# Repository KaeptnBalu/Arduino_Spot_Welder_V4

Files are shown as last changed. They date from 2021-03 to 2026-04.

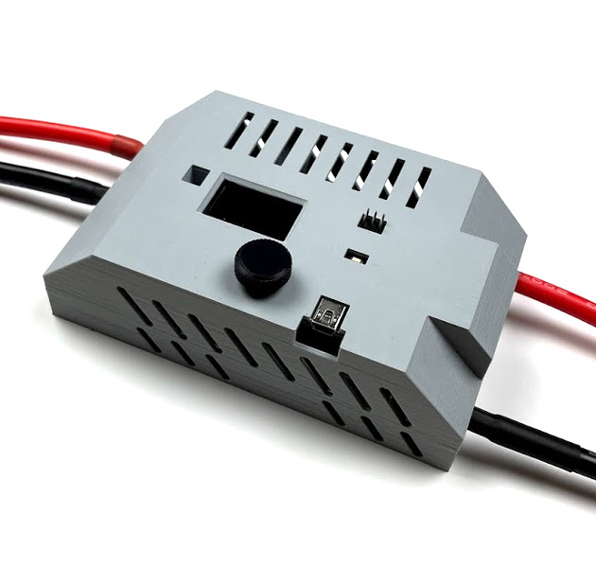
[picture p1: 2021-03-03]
Parts/Spot_Welder_V4_Case/case_kit_v4.jpg

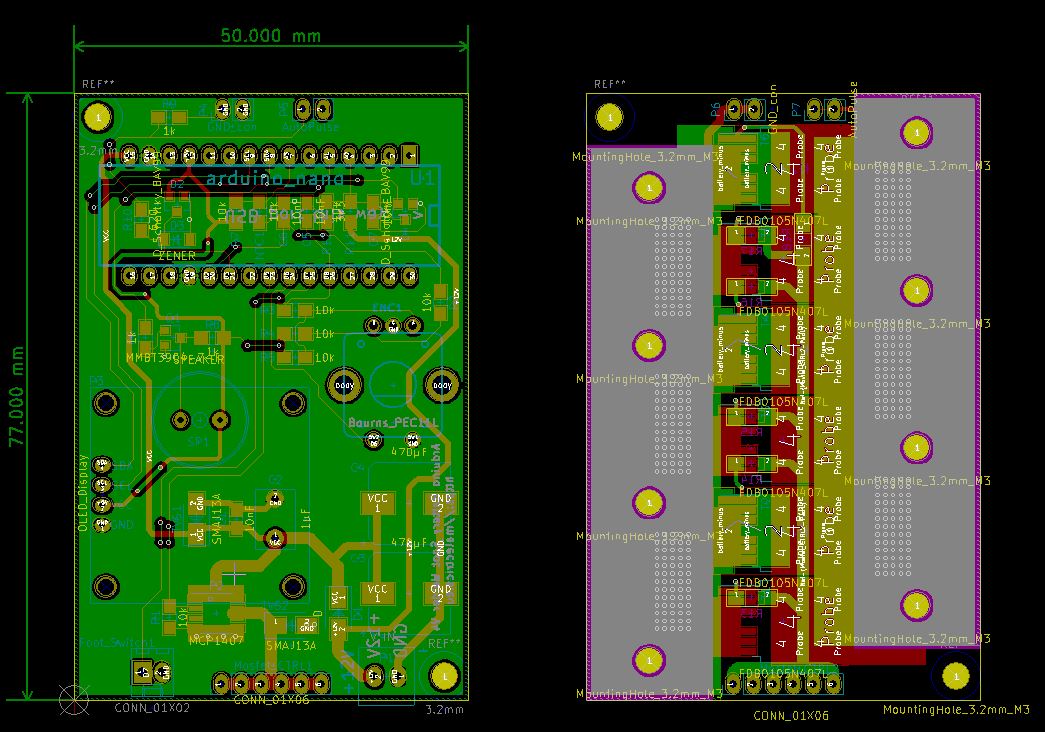
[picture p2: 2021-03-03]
KiCAD_PCB_Files/Spot_Welder_V4_PCB_Layout.JPG

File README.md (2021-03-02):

# Arduino_Spot_Welder_V4
This is the latest V4 of the Arduino Spot Welder. The previous V3 can be found here https://github.com/KaeptnBalu/Arduino_Spot_Welder_V3

An Arduino based Spot Welder for battery welding

    Build Guide: Car Bundle: https://malectrics.eu/v4-car-battery-bundle-assembly-instructions/ 
                 Lipo Bundle:https://malectrics.eu/v4-lipo-battery-bundle-assembly-instructions/
    Introduction Video: coming soon (Video for previuos V3 https://www.youtube.com/watch?v=CNmvx2JSCvA)
    Project Homepage: https://malectrics.eu/

Improvements in V4:

- Buzzer: With the buzzer alarms will not only be displayed on the screen but also be audible for the user. This makes it much easier to notice an alarm while working with the welder.    
- Temperature Sensor: The temperature sensor will trigger an alarm and disable welding when temperature reaches 65°C to protect the welder from overheating.
- additional 470µF Capacitor: With now two 470µF capacitors it is possible to use weld times up to 100 – 150ms without the risk of the Arduino Nano rebooting. The reboot could happen in V3 at very long weld times because the voltage at the Arduino Nano dropped to low dring the weld.  
- SMD Mosfet Driver: the mosfet driver chip has been changed from the through hole version that was plugged in a socket to a SMD version that is directly soldered to the pcb. The SMD version eliminates eventual contact problems that could happen with the through hole version when it was not plugged in the socket correctly.
- SMD Mosfets: The mosfets have been changed from through hole version to SMD. That will eliminate the problem of failing mosfet legs in V3 on very high currents.
- new aluminum parts: there are still two aluminum parts used on the mosfet board but the parts are just straight and both the same size. This makes producing or modding them for DIY users much easier.    
- Stronger Protection Diodes: The protection diodes on the bottom of the mosfet board have been changed to a much stronger version. They are rated for the same current as the ones in V3 but can take much higher short peak amps and have better heat dissipation because they are phisically bigger.

This Spot Welder can be used to weld 18650 batteries. It uses a 12V car battery as welding current supply. Typically one 60Ah 600A battery delivers enough current to get good welds with 0.15mm - 0.2mm nickel strips. For thicker nickel strips maybe you will need bigger battery or two in paralell. (Maximum 800A total)

The Welder generates a double pulse, where the first one is 12% of the time of the second one by default. Pulse time of the main pulse is adjustable by the rotary encoder and displayed on the screen in ms so you can exactly adjust the time. Its adjustable from 1 … 100 mS by default. (adjustable up to 500ms in the system menu)

If you want to download the project click on "clone or download" on this page. Downloading single files sometimes seems to cause some files to be corrupted while downloading.

You can get parts to build your own Spot Welder or prebuilt kits at https://malectrics.eu/

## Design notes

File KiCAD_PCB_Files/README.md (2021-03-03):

These are the pcb files for the Spot welder V4

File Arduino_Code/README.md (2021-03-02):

This is the Arduino Code for the Spot Welder V4. Do not use it with the older V2 or V3 pcbs. It is not compatible with these.

You need to have the Ardafruit_GFX library and the Ardafruit_SSD1306 library installed in your Arduino IDE to sucessfully compile the Code.

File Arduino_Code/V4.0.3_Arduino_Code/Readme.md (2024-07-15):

This is the V4.0.3 Arduino Code for the Arduino Spot Welder.

Improvements:
 - updated the menue structure 
 - added weld activation sound 
 - added a sound in auto pulse mode when both welding tips touch the nickel
 - sound can be switched on and off in the menue

After updating to this version please perform a "Full Reset" in the system menue of the welder to ensure proper functionality.

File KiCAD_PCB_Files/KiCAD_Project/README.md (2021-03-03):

These are the KICAD project files for the Arduino Spot Welder V4

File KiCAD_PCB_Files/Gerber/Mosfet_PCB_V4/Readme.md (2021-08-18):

These are the Gerber files for the Mosfet PCB V4. Please order it with 4oz copper layer at the pcb manufacturer because it needs to take a lot of current.

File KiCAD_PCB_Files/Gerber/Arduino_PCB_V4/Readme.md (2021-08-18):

These are the gerber files for the Arduino PCB V4. This one can be ordered with the standard 1oz copper layer.

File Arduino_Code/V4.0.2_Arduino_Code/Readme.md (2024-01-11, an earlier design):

This is the V4.0.2 Arduino Code for the Arduino Spot Welder.

Improvements:
- minor code improvements

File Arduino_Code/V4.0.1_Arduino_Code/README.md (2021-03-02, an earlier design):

This is the initial release of the redesigned V4.0.1 Arduino Code for the Arduino Spot Welder.

Improvements:
- adjust Code to work with Spot Welder V4
- add Buzzer routines
- add temperature sensor routines

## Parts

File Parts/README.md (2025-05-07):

These are the parts you need to buy for building the Spot Welder V4 from scratch. With the Mouser.com Shop Link you can directly ad all electronic component parts to your shopping cart.

Not included in the Mouser shopping cart link:

    1x Arduino Nano
    1x OLED Display

You can get ready made welding cables, aluminum parts and pcb sets at www.malectrics.eu if you dont want to make them yourself.

# BOM (Bill of materials) - electronic components

|Quantity |PCB Reference |Name |Mouser.com Part Number |
|---|---|---|---|
|6 |IRFS7430TRL7PP |Mosfet IRFS7430TRL7PP 40V 522A |942-IRFS7430TRL7PP |
|1 |MCP1407 |Mosfet Driver MCP1407-E/SN |579-MCP1407-E/SN |
|1 |Bourns_PEC11L |Rotary Encoder |652-PEC11L4220FS0015 |
|2 |U1 Arduino Nano |1x15 Pol Female Pin Header |992-15FX1-254MM |
|1 |Mosfet_CTRL2 |1x8 Pol Female Pin Header |437-8018700810001101 |
|2 |P6,P7 |1x2 Pol Female Pin Header |437-8018700210001101 |
|1 |OLED_Display |1x4 Pol Female Pin Header |517-974-01-04-RK |
|1 |Mosfet_CTRL1, P4, P5  |1x16 Pol Male Pin Header |538-22-28-4160 |
|1 |Foot_Switch1 |PCB connector 2pin |710-61900211121 |
|1 |P1 |Terminal Block |710-691214110002 |
|1 |D1 |SMD-Schottky 60V 1A |750-CDBA160-G |
|1 |Zener D3 |SMD Zener diode 4,3V 0,5W |78-MMSZ4687-E3-08 |
|2	 |D2,D4	 |Schottky BAV99	 |78-BAV99-E3-08 |
|4	 |TVS3,TVS4,TVS5	 |TVS Diode 15,6V 7kW	 |576-SLD8S14A |
|1	 |TVS1,TVS2	 |TVS Diode 14,4V 400W	 |621-SMAJ13A-13-F |
|1	 |C2	 |film capacitor 1 µF RM5	 |505-MKS2C041001FMSSD |
|2 |C3,C4 |electrolytic capacitor 470µF 25V |647-UWT1E471MNL1S |
|4 |C1, C5, C6, C7 |ceramic capacitor 0,01µF SMD |80-C0805C103J5R |
|1 |Q1 |Bipolartransistor 200mA |621-MMBT3904-F |
|1 |SP1 |Piezzo Speaker |810-PS1240P02BT |
|1 |NTC1 |NTC Thermistor |81-NCP21XV103J03RA |
|10 |R1;R2,R3,R4,R5,R7,R11 |Resistor 0805 SMD  10 kOhm |603-RC0805FR-0710KL |
|10 |R6,R8,R9 |Resistor 0805 SMD  1 kOhm |603-RC0805FR-071KL |
|10 |R10 |Resistor 0805 SMD  620 Ohm |603-RC0805FR-07620RL |
|10 |R12 |Resistor 0805 SMD  3,3 kOhm |603-RC0805FR-133K3L |
|10 |R13 … R18 |Resistor 1206 SMD  30 Ohm |603-RC1206FR-0730RL |

## Other Parts - Mechanical Parts - Optional Parts

| Quantity | Name | Description | Link / Where to buy |
|---|---|---|---|
| 1 | Arduino Nano | | [Banggood](https://ban.ggood.vip/15P6G)|
| 1 | OLED Diplay 0,96" 128x64 | take care of correct pinout (GND - VCC - SCL - SDA) | [Banggood](https://ban.ggood.vip/15P6J) |
| 1 | Alu 90x15x4mm | see alu_template.pdf | local hardware Store or  https://malectrics.eu/  | 
| 8 | M3x8 screw + nuts | for Alu Parts assembly | local hardware store |
| 2 | M3x20 screw | to screw pcbs together | local hardware store |
| 6 | M3 Nylon Nuts | to screw pcbs together | Ebay or Aliexpress |
| 1 | 1m 10 mm² - 16mm² flexible silicone cable | for 2pcs 0,5m welding cables | Ebay or Aliexpress |
| 1 | 0,1m 10mm² - 16mm² solid copper wire | for the welding tips | local hardware store or welding tips from https://malectrics.eu/ |
| 2 | cable shoe for 10 mm² or 16mm2 | for welding cable | local hardware store or https://malectrics.eu/ |
| 2 | cable connector for 10 mm² or 16mm2 | welding tip connection to the welding cables | local hardware store or https://malectrics.eu/ |
| 1 | battery terminals | for car battery | local hardware store or https://malectrics.eu/ |
| 1 | PCB Set | Arduino + Mosfet PCB | https://malectrics.eu/ |
| 2 | nylon spacers M2 x 12mm + M2x5 screws for OLED display | OPTIONAL | Ebay or Aliexpress |
| 1 | Foot Switch | OPTIONAL | https://malectrics.eu/ |
| 1 | 3d printed case | OPTIONAL | https://malectrics.eu/ or [Github](https://github.com/KaeptnBalu/Arduino_Spot_Welder_V4/tree/main/Parts/Spot_Welder_V4_Case) |
| 1 | 300A Fuse | OPTIONAL | https://malectrics.eu/

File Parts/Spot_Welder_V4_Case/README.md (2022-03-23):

These are the CAD files for the case. You can use these if you want to modify the case for your needs. The case was designed in Autodesk Fusion 360.
Ready printed case with acessories can be bought here: https://malectrics.eu/product/arduino-spot-welder-v4-case-kit-copy/

Additional hardware you need to mount the welder and the ANL 300A fuse in the case:

- 30x30x10mm 12V fan
- 4pcs M3x16 screws
- 2pcs M5x10mm screws
- 2pcs M5 nuts
- 2pcs M5 washers
- 2pcs M5 brass washers

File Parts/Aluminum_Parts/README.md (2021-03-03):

Use the PDF template to cut the aluminum pieces from 4mm material.
The parts can be mounted to the pcb with M3x8 screws and M3 nuts.

You can also take a look at the dxf drawing to manufacture the aluminum parts with a cnc or something else.

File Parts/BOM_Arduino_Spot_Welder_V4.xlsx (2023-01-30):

BOM Arduino Spot Welder V4
 |  | Mouser.com Parts
Quantity | PCB Reference | Name | Mouser.com Part Number | Note
6 | IRFS7430TRL7PP | Mosfet IRFS7430TRL7PP 40V 522A | 942-IRFS7430TRL7PP (https://www.mouser.de/ProductDetail/942-IRFS7430TRL7PP)
1 | MCP1407 | Mosfet Driver MCP1407-E/SN | 579-MCP1407-E/SN (https://www.mouser.de/ProductDetail/579-MCP1407-E-SN)
1 | Bourns_PEC11L | Rotary Encoder | 652-PEC11L4220FS0015 (http://www.mouser.de/Search/ProductDetail.aspx)
2 | U1 Arduino Nano | 1x15 Pol Female Pin Header | 992-15FX1-254MM (http://www.mouser.de/Search/ProductDetail.aspx)
1 | Mosfet_CTRL2 | 1x8pol female header | 437-8018700810001101 (http://www.mouser.de/Search/ProductDetail.aspx)
2 | P6,P7 | 1x2pol female header | 437-8018700210001101 (http://www.mouser.de/Search/ProductDetail.aspx)
1 | OLED_Display | 1x4pol female header | 517-974-01-04-RK (http://www.mouser.de/Search/ProductDetail.aspx)
1 | Mosfet_CTRL1, P4, P5 | 1x16 Pol Male Pin Header | 538-22-28-4160 (http://www.mouser.de/Search/ProductDetail.aspx)
1 | Foot_Switch1 | PCB connector 2pin | 710-61900211121 (http://www.mouser.de/Search/ProductDetail.aspx)
1 | P1 | Terminal Block | 710-691214110002 (https://www.mouser.de/ProductDetail/710-691214110002)
1 | D1 | SMD-Schottky 60V 1A | 750-CDBA160-G (http://www.mouser.de/Search/ProductDetail.aspx?R=CDBA160-Gvirtualkey59960000virtualkey750-CDBA160-G)
1 | Zener D3 | SMD Zener diode 4,3V 0,5W | 78-MMSZ4687-E3-08 (http://www.mouser.de/Search/ProductDetail.aspx)
2 | D2,D4 | Schottky BAV99 | 78-BAV99-E3-08 (https://www.mouser.de/ProductDetail/78-BAV99-E3-08)
4 | TVS3,TVS4,TVS5 | TVS Diode 15,6V 7kW | 576-SLD8S14A (https://www.mouser.de/ProductDetail/576-SLD8S14A)
1 | TVS1,TVS2 | TVS Diode 14,4V 400W | 621-SMAJ13A-13-F (http://www.mouser.de/Search/ProductDetail.aspx)
1 | C2 | film capacitor 1 µF RM5 | 505-MKS2C041001FMSSD (http://www.mouser.de/Search/ProductDetail.aspx)
4 | C1, C5, C6, C7 | ceramic capacitor 0,01µF SMD | 80-C0805C103J5R (https://www.mouser.de/ProductDetail/80-C0805C103J5R)
1 | C3,C4 | electrolytic capacitor 470µF 25V | 647-UWT1E471MNL1S (http://www.mouser.de/Search/ProductDetail.aspx)
1 | Q1 | Bipolartransistor 200mA | 621-MMBT3904-F (https://www.mouser.de/ProductDetail/621-MMBT3904-F)
1 | SP1 | Piezzo Speaker | 810-PS1240P02BT (https://www.mouser.de/ProductDetail/810-PS1240P02BT)
1 | NTC1 | NTC Thermistor | 81-NCP21XV103J03RA (https://www.mouser.de/ProductDetail/81-NCP21XV103J03RA)
10 | R1;R2,R3,R4,R5,R7,R11 | Resistor 0805 SMD 10 kOhm | 603-RC0805FR-0710KL (https://www.mouser.de/ProductDetail/Yageo/AC1206FR-071KL?qs=sGAEpiMZZMu61qfTUdNhG19HzxXL1i6itFKVZ7nWm2k%3D)
10 | R6,R8,R9 | Resistor 0805 SMD 1 kOhm | 603-RC0805FR-071KL (https://www.mouser.de/ProductDetail/603-RC0805FR-071KL)
10 | R10 | Resistor 0805 SMD 620 Ohm | 603-RC0805FR-07620RL (https://www.mouser.de/ProductDetail/603-RC0805FR-07620RL)
10 | R12 | Resistor 0805 SMD 3,3 kOhm | 603-RC0805FR-133K3L (https://www.mouser.de/ProductDetail/603-RC0805FR-133K3L)
10 | R13 … R18 | Resistor 1206 SMD 30 Ohm | 603-RC1206FR-0730RL (https://www.mouser.de/ProductDetail/603-RC1206FR-0730RL)
 |  |  | Other Parts
Quantity |  | Name | Description | Link / Where to buy
1 |  | Arduino Nano |  | https://www.banggood.com/de/Geekcreit-ATmega328P-Nano-V3-Controller-Board-Improved-Version-Module-Development-Board-p-940937.html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
1 |  | OLED Diplay 0,96" 128x64 | take care of correct pinout (GND - VCC - SCL - SDA) | https://www.banggood.com/Geekcreit-0_96-Inch-OLED-I2C-IIC-Communication-Display-128+64-LCD-Module-Geekcreit-for-Arduino-products-that-work-with-official-Ardui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
1 |  | Alu 90*15*4mm | see alu_template.pdf (https://github.com/KaeptnBalu/Arduino_Spot_Welder_V4/blob/main/Parts/Aluminum_Parts/Alu_Parts_V4.pdf) | local hardware Store or https://malectrics.eu/
8 |  | M3x8 screw + nuts | for Alu Parts assembly | local hardware store
2 |  | M3x20 screw | to screw pcbs together | local hardware store
6 |  | M3 Nylon Nuts | to screw pcbs together | Ebay or Aliexpress
1 |  | 1m 10 mm² - 16mm² flexible silicone cable | for 2pcs 0,5m welding cables | Ebay or Aliexpress
1 |  | 0,1m 10mm² - 16mm² solid copper wire | for the welding tips | local hardware store or welding tips from https://malectrics.eu/
2 |  | cable shoe for 10 mm² or 16mm2 | for welding cable | local hardware store or https://malectrics.eu/
2 |  | cable connector for 10 mm² or 16mm2 | welding tip connection to the welding cables | local hardware store or https://malectrics.eu/
1 |  | battery terminals | for car battery | local hardware store or https://malectrics.eu/
1 |  | PCB Set | Arduino + Mosfet PCB | https://malectrics.eu/
2 |  | nylon spacers M2 x 12mm + M2x5 screws for OLED display | OPTIONAL | Ebay or Aliexpress
1 |  | Foot Switch | OPTIONAL | https://malectrics.eu/
1 |  | 3d printed case | OPTIONAL | https://github.com/KaeptnBalu/Arduino_Spot_Welder_V4/tree/main/Parts/Spot_Welder_V4_Case
1 |  | 300A Fuse | OPTIONAL | https://malectrics.eu/

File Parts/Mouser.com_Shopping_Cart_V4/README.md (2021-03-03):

https://www.mouser.com/ProjectManager/ProjectDetail.aspx?AccessID=6572a2786f

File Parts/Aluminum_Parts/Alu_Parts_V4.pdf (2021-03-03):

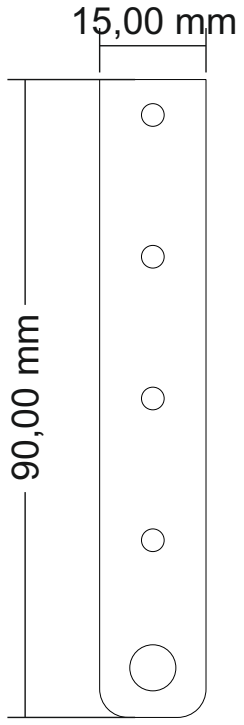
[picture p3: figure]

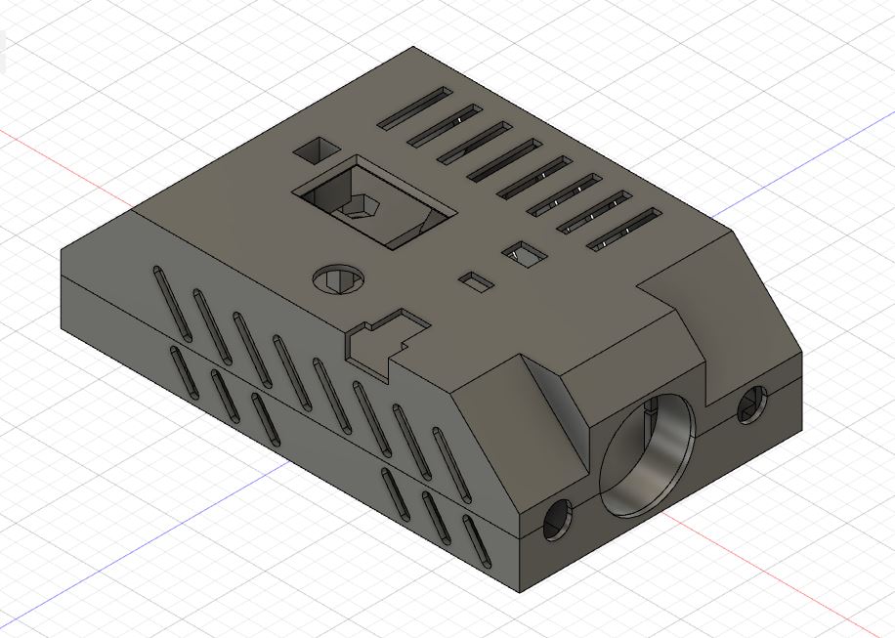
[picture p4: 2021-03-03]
Parts/Spot_Welder_V4_Case/Arduino_Spot_Welder_V4_Case_3d.JPG

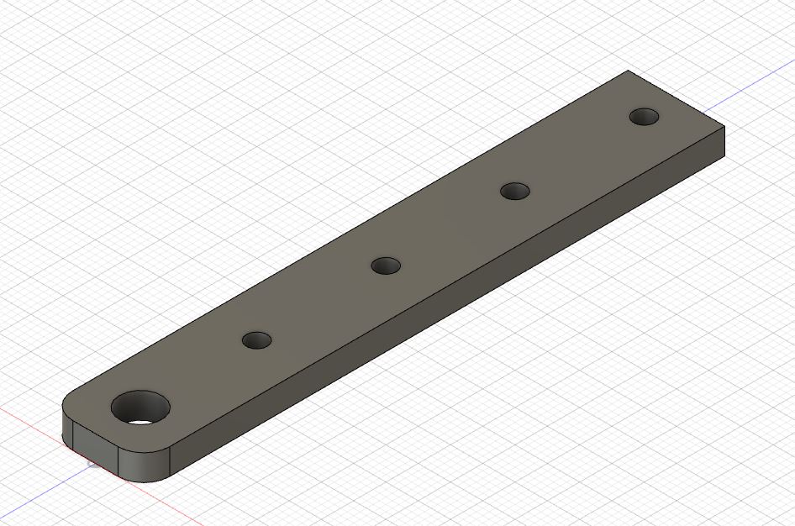
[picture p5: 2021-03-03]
Parts/Aluminum_Parts/Alu_Part_V4_3d.JPG

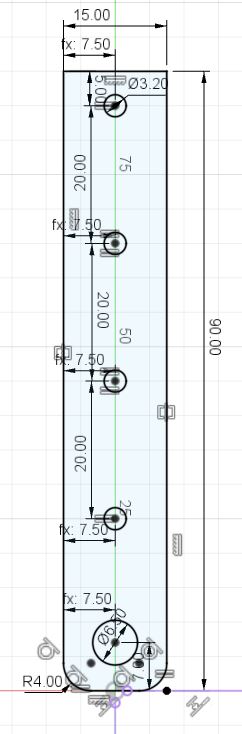
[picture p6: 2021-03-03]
Parts/Aluminum_Parts/Alu_Part_V4_sketch.JPG

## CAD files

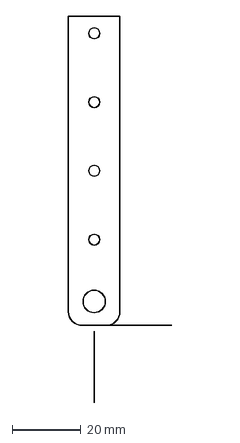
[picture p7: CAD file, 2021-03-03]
Parts/Aluminum_Parts/Alu_Part_V4_4mm.dxf
30.0 x 112.5 mm

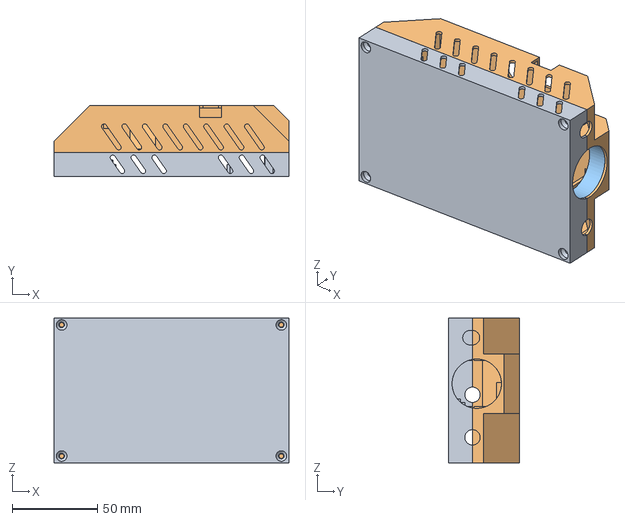
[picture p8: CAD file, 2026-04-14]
Parts/Spot_Welder_V4_Case/Arduino_Spot_Welder_V4_Case.step
138.0 x 41.5 x 85.0 mm

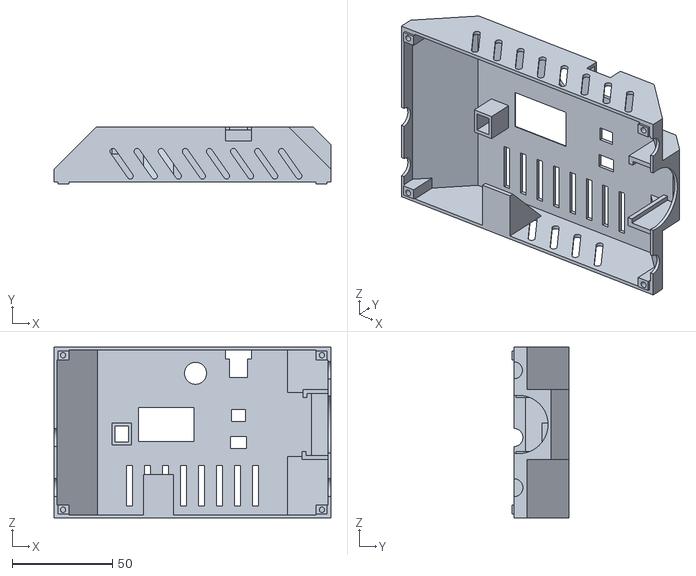
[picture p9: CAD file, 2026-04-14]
Parts/Spot_Welder_V4_Case/STL_3D_Printing/Arduino_Spot_Welder_V4_Case_Top.stl
138.0 x 28.5 x 85.0

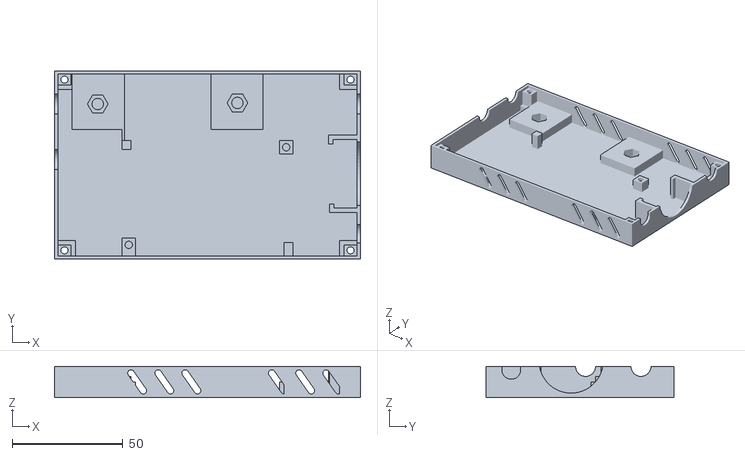
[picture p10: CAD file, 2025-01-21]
Parts/Spot_Welder_V4_Case/STL_3D_Printing/Arduino_Spot_Welder_V4_Case_Bottom.stl
138.0 x 85.0 x 14.0

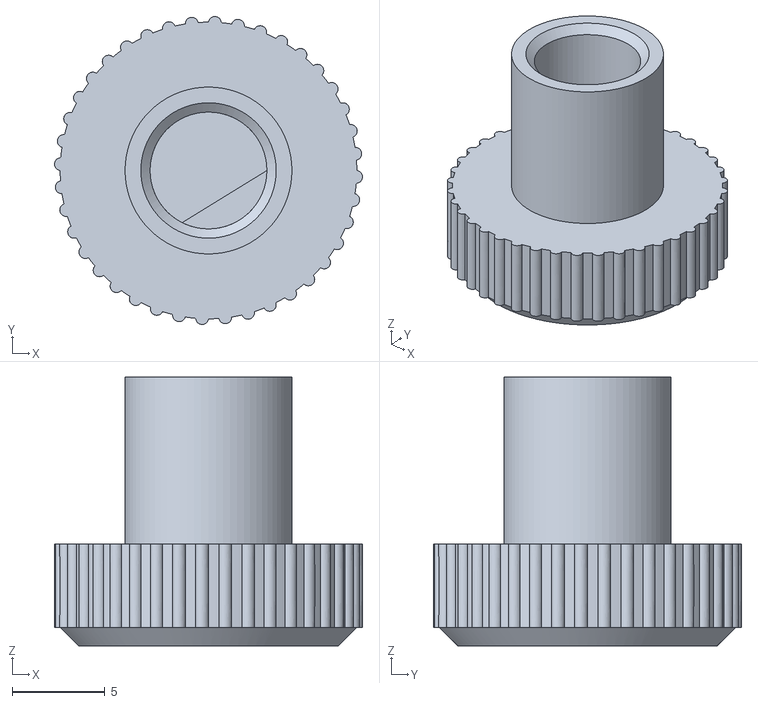
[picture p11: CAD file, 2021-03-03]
Parts/Spot_Welder_V4_Case/STL_3D_Printing/Rotary_Knob.stl
16.6 x 16.6 x 14.5

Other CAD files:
Parts/Spot_Welder_V4_Case/Arduino_Spot_Welder_V4_Case.f3d

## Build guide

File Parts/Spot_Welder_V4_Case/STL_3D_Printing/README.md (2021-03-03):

These are the STL files of the case for 3d printing. 

Printing Parameters I used:
- PLA material
- no support
- 0.2mm layer height

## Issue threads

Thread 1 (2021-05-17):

LiFePO4 Batteries

DanielMarcato, 2021-05-17:
Hi,

no other idea how to ask this question so I will try to get an answer via an "issue".

Do you think the new V4 can handle car batteries made from LiFePO4 cells?
I have access to one made of four 280Ah cells in series which gives a ~13.4V total.
Current rating from the manufacturer is 280A continuously and I don't have any information on pulse capabilities but my guess is that the lithium version could be much more powerful than an average car battery.

Looking forward to your response!

Best,
Daniel

BTW: Just ordered one - the V4 looks really good. I will retire the V1 that I got a couple years back.

KaeptnBalu, 2021-05-18:
Hi,
I have no acess to such a lithium car battery, so dont know how much max. current it can put out.
The welder can handle up to 800A no problem. Maybe even up to 1000A could be fine.
Also you need to check if your lifepo4 battery is protected by a bms. Then it is possible that your battery is shut down after every weld because of over current / short circuit protection.

DanielMarcato, 2021-05-18:
BMS is installed but I put the V1 welder directly to the battery terminals thus circumventing the BMS. The V1 died (first the TVS diodes that I had installed and then one of the FET driver chips) which is why I ordered the V4 now.

Maybe a list in your repositories with successful battery setups would be useful - people could post their batteries and weld times to get a feeling for good brands etc.

DanielMarcato, 2021-05-23:
Worked perfectly with the Lifepo - great product!

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

Closed 2021-05-23.

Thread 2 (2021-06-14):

Unrouted/Unconnected Item in Mosfet board -

bantybanty, 2021-06-14:
Hi,

Firstly thank you for making the PCB and supported code.

Problem 1.
I am very new to Kicad. After opening the project and plotting Gerber files, I clicked Run DRC and found these items. Please verify the pads and their nets.
http://prntscr.com/15djesk

Problem 2.
On JLPCB Website  "Can not identify the board outline"
https://prntscr.com/15dlfii

Siddharth

KaeptnBalu, 2021-06-15:
Hi,
You need to do gerber files for both boards seperately. I do this by saving a copy of the Arduino_Spot_Welder_Kicad.pcb file as "Arduino_Board.pcb", then delete the mosfet board from it and then do the gerber creation. Do the same for the mosfet board. Also make sure when you order pcbs to get the mosfet board with at least 4 oz copper layer. A thinner copper layer will fail very quickly because of the high current.

Closed 2024-07-03.

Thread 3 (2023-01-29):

Some corrections in excel BOM and mouser basket

Nick-Z0, 2023-01-29:
Hey Marc, first of all thanks for this great product!

I have found a couple of issues in the provided BOM excel file listed below:

**Excel BOM**
```
Line            Problem
6		mosfet quantity 6 instead of 8 (for new version)
17		1 schotky instead of 2
16		IC socket not needed
22		film capacitor 1μF RM5
20		TVS diode (updated in new version?)
24		capacitor not in stock (I used this one as a replacement: 661-EMZL250ARA471MJA)

```
**Mouser basket issues**
3.3k Ohm resistor wrong quantity 10 instead of 1 (?)
Maybe also add optional 12V 30x30mm fan link

I also have a question. Will a thicker cable be any improvement for the welder?

KaeptnBalu, 2023-01-31:
Thanks for pointing this out. I fixed the errors in the BOM.
The capacitor you chose as replacement for the out of stock one should work fine.

Mouser basket issues:
There is just 1 resistor 3.3k Ohm necessary. Anyway i changed the quantity to 10 in the basket so now all resistors are listed with quantity 10 to have spare.

Thicker cable can be used if you need longer than the standard 50cm welding leads. For the standard 50cm it is not necessary to go with thicker cables.

Nick-Z0, 2023-01-31:
Do you have a schematic or instructions for the PCB assembly? Or are the BOM descriptions (excel file) sufficient?

Also, I could not edit the mouser basket because I already had some parts. I had to share it to myself and then I could edit it.

KaeptnBalu, 2023-02-01:
There is no assembly instructions for the pcbs.
But you can find the schematic and pcb layout here: https://github.com/KaeptnBalu/Arduino_Spot_Welder_V4/tree/main/KiCAD_PCB_Files
The "PCB Reference" mentioned in the BOM is printed on the pcbs for every part, so it is pretty easy to populate the pcbs.

Closed 2024-07-03.

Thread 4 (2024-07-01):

No sound on weld connection and after weld. (More of a suggestion)

420pootang69, 2024-07-01:
I've used some of the cheaper welders over the years and they always give an audible indication of the weld taking place. Seemed weird it wasn't on here. I also wanted one when the probes where detected.

Maybe it's just me, but I really prefer the additional audio feedback.

I did a quick hack on mine, just including the code to show you what I mean.

	if ( shortPulseDelay < 1 ) shortPulseDelay = 1;

	tone(PIN_BUZZ, 1000, 200);

	// Wait the pulse engagement delay time.
	if ( sensePin == PIN_AUTO_PULSE ) {
		wait.opt = PGR_ON;
		wait.time = delayEngage;

		while ( !drawProgress( &wait, false ) ) {
			if ( digitalRead( PIN_AUTO_PULSE ) != activePinState ) {
				drawProgress( &wait, true );
				return;
			}
		}
	} else {
		delay( delayEngage );
	}

	tone(PIN_BUZZ, 1000, 200);

	if ( pData.shortPulseTime > 0 && pData.pulseTime > 3 ) {
		// Send the pre-heat pulse.
		weldPulse( P_ON );
		delay( shortPulseDelay );
		weldPulse( P_OFF );

		// Wait the inter-pulse delay time.
		delay( shortPulseDelay );
	}

As I said, just a suggestion for a software update going forward.

Closed 2024-07-03.

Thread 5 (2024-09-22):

Using Cap Bank

BenJBachler, 2024-09-22:
I would like mod this use a capacitor bank as a current source and a lab bench power supply as a power source instead of a battery. I'm thinking of adding a 3rd board to mount the capacitors and a mosfet to disconnect the power supply once charged. Is there an engineering reason this wasn't done before and would it be possible to integrate this into your design?

KaeptnBalu, 2024-09-23:
It was not done yet because the necessary capacitor bank to deliver enough power is much more expensive than a car battery or lipo. There is no technical reason against this idea.

BenJBachler, 2024-09-24:
This is more in depth than I thought, if you don't mind helping with this. The battery pack would provide constant voltage and the max current that the welding surface will allow while a CD welder's voltage would drop as the charge is drained. How much does this affect the weld? I am thinking about taking the route shown [here](https://www.zeva.com.au/Projects/SpotWelderV2/) and replace your Mosfet board. I think I would have to tailor your code to make this work though. Another idea that would be simpler would be to use a dewalt battery and a regulator board to provide the VCC voltage for the nano but I don't think the mosfet can handle the extra voltage (dewalt is 20V). Would using a dewalt battery be too much voltage?

BenJBachler, 2024-10-14:
Closing

Closed 2024-10-14.

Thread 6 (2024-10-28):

copper weight Mosfet board

champagnecharly, 2024-10-28:
Hi, thank you for providing this. It will be my first project even if all the hard work has been already done. I am looking to use jlcpcb however their maximum copper weight is 2oz What are your thoughts on increasing the number of layers with copies of the current and joining those to allow for more current?  heir default internal layers is 0.5oz. They do also have a copper core option for improved current/heat dissipation.   however for these the outer layer is only 1oz and there is not information on the inner layer thickness. Thanks in advance. I wish Brexit had never happened.

Closed 2024-11-08.

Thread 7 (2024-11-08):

footprint library missing

champagnecharly, 2024-11-08:
the following lib appears to be missing:

(fp_lib_table
  (lib (name pots_own)(type KiCad)(uri E:\Cloud\SkyDrive\Own_Kicad_Libraries\pots_own.pretty)(options "")(descr ""))
  (lib (name Rotary-Encoders)(type KiCad)(uri E:\Cloud\SkyDrive\Own_Kicad_Libraries\Rotary-Encoders.pretty)(options "")(descr ""))
  (lib (name OLED_SSD1306)(type KiCad)(uri E:\Cloud\SkyDrive\Own_Kicad_Libraries\OLED_SSD1306.pretty)(options "")(descr ""))
  (lib (name Vias)(type KiCad)(uri E:\Cloud\SkyDrive\Own_Kicad_Libraries\Vias.pretty)(options "")(descr ""))
  (lib (name smd-semi)(type KiCad)(uri E:\Cloud\SkyDrive\Own_Kicad_Libraries\kicad-pcblib-master\smd-semi.pretty)(options "")(descr ""))
  (lib (name Connectors_USB)(type KiCad)(uri E:\Cloud\SkyDrive\Own_Kicad_Libraries\Connectors_USB.pretty)(options "")(descr ""))
  (lib (name arduino)(type Legacy)(uri E:\Cloud\SkyDrive\Own_Kicad_Libraries\Arduino_nano.pretty\arduino.mod)(options "")(descr ""))
)

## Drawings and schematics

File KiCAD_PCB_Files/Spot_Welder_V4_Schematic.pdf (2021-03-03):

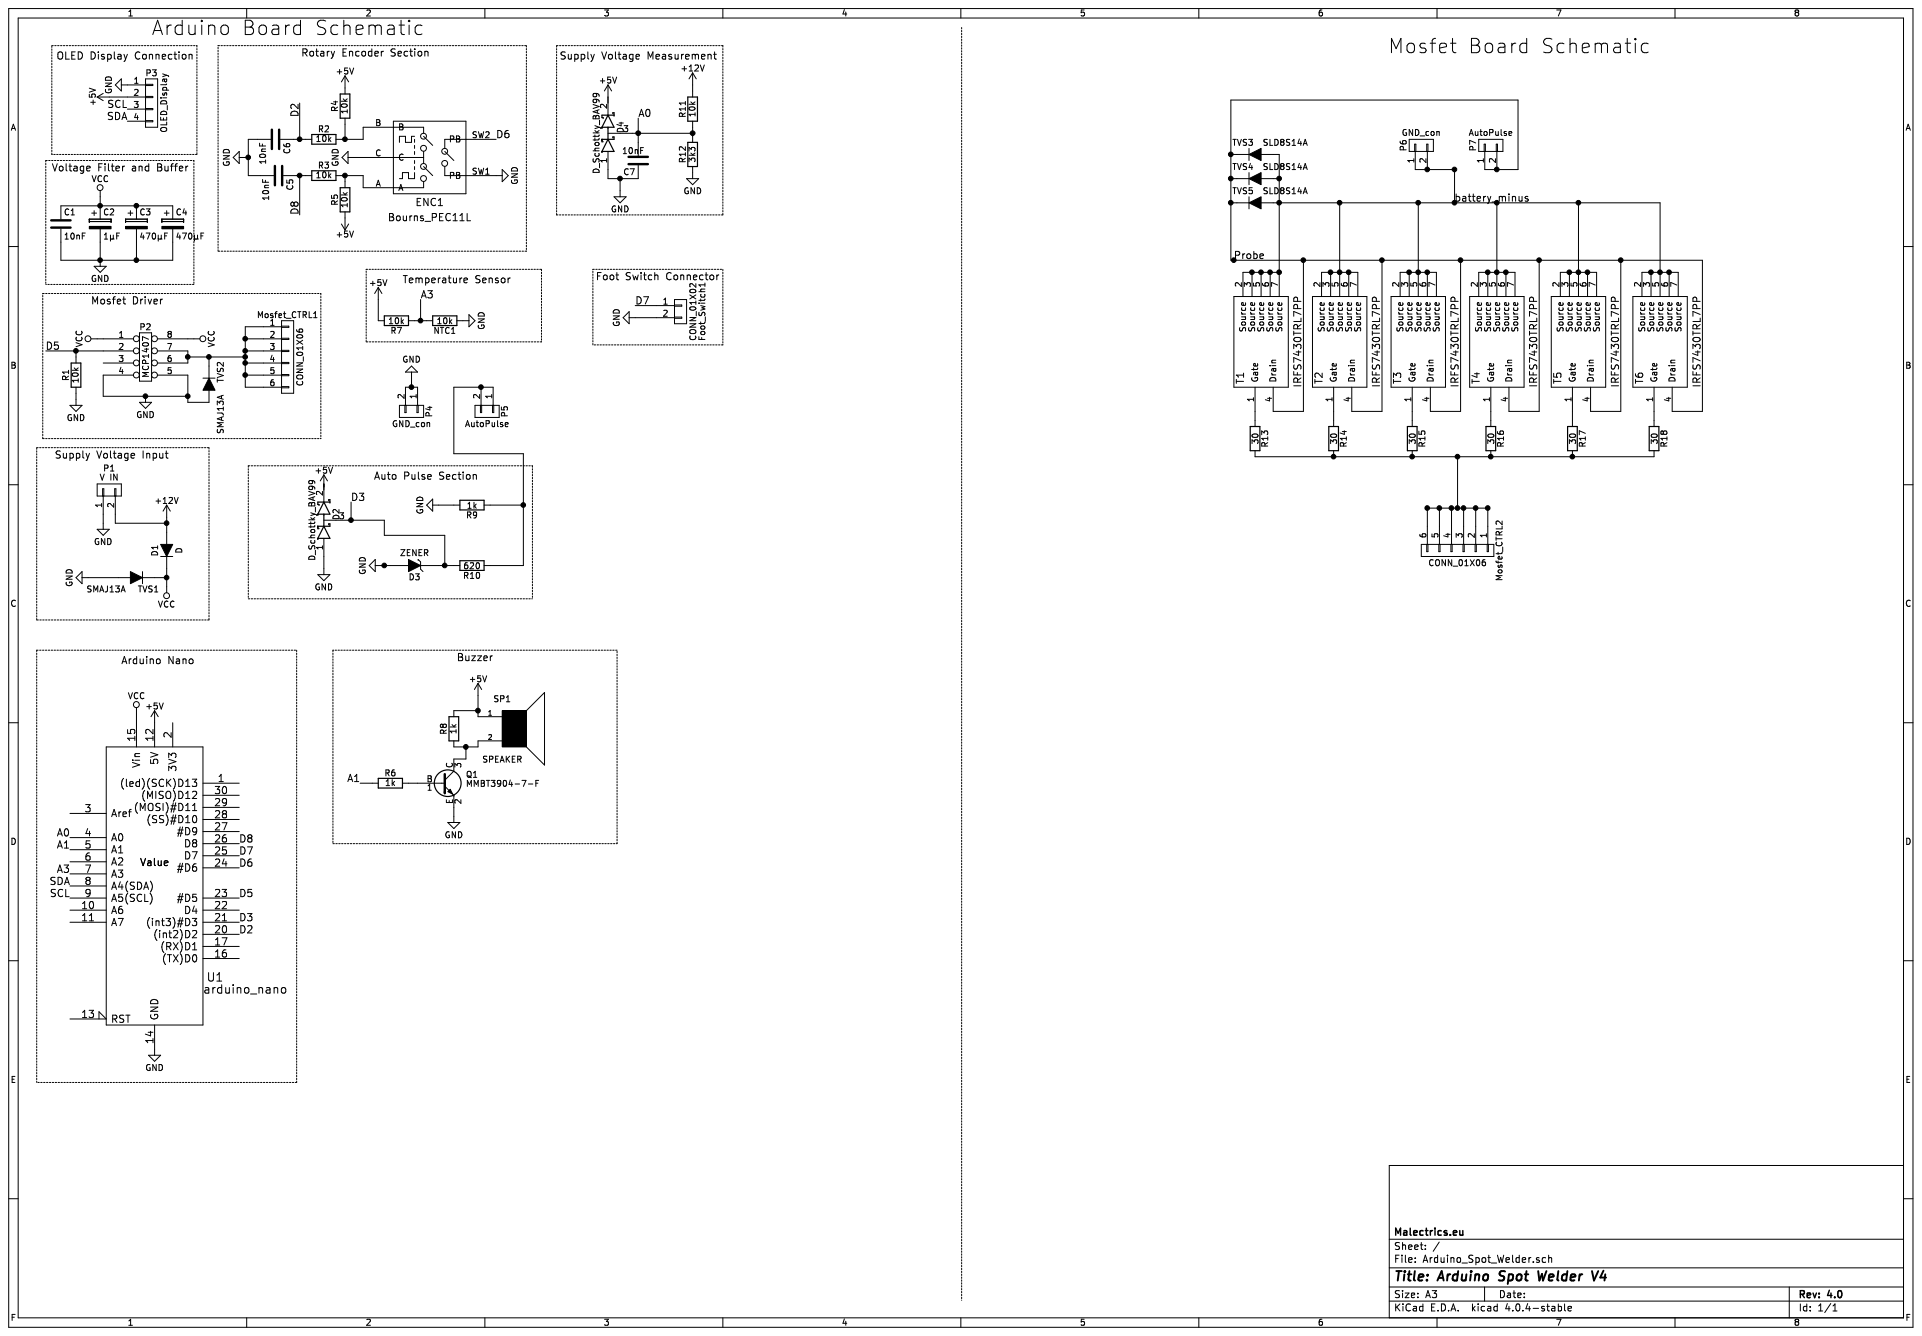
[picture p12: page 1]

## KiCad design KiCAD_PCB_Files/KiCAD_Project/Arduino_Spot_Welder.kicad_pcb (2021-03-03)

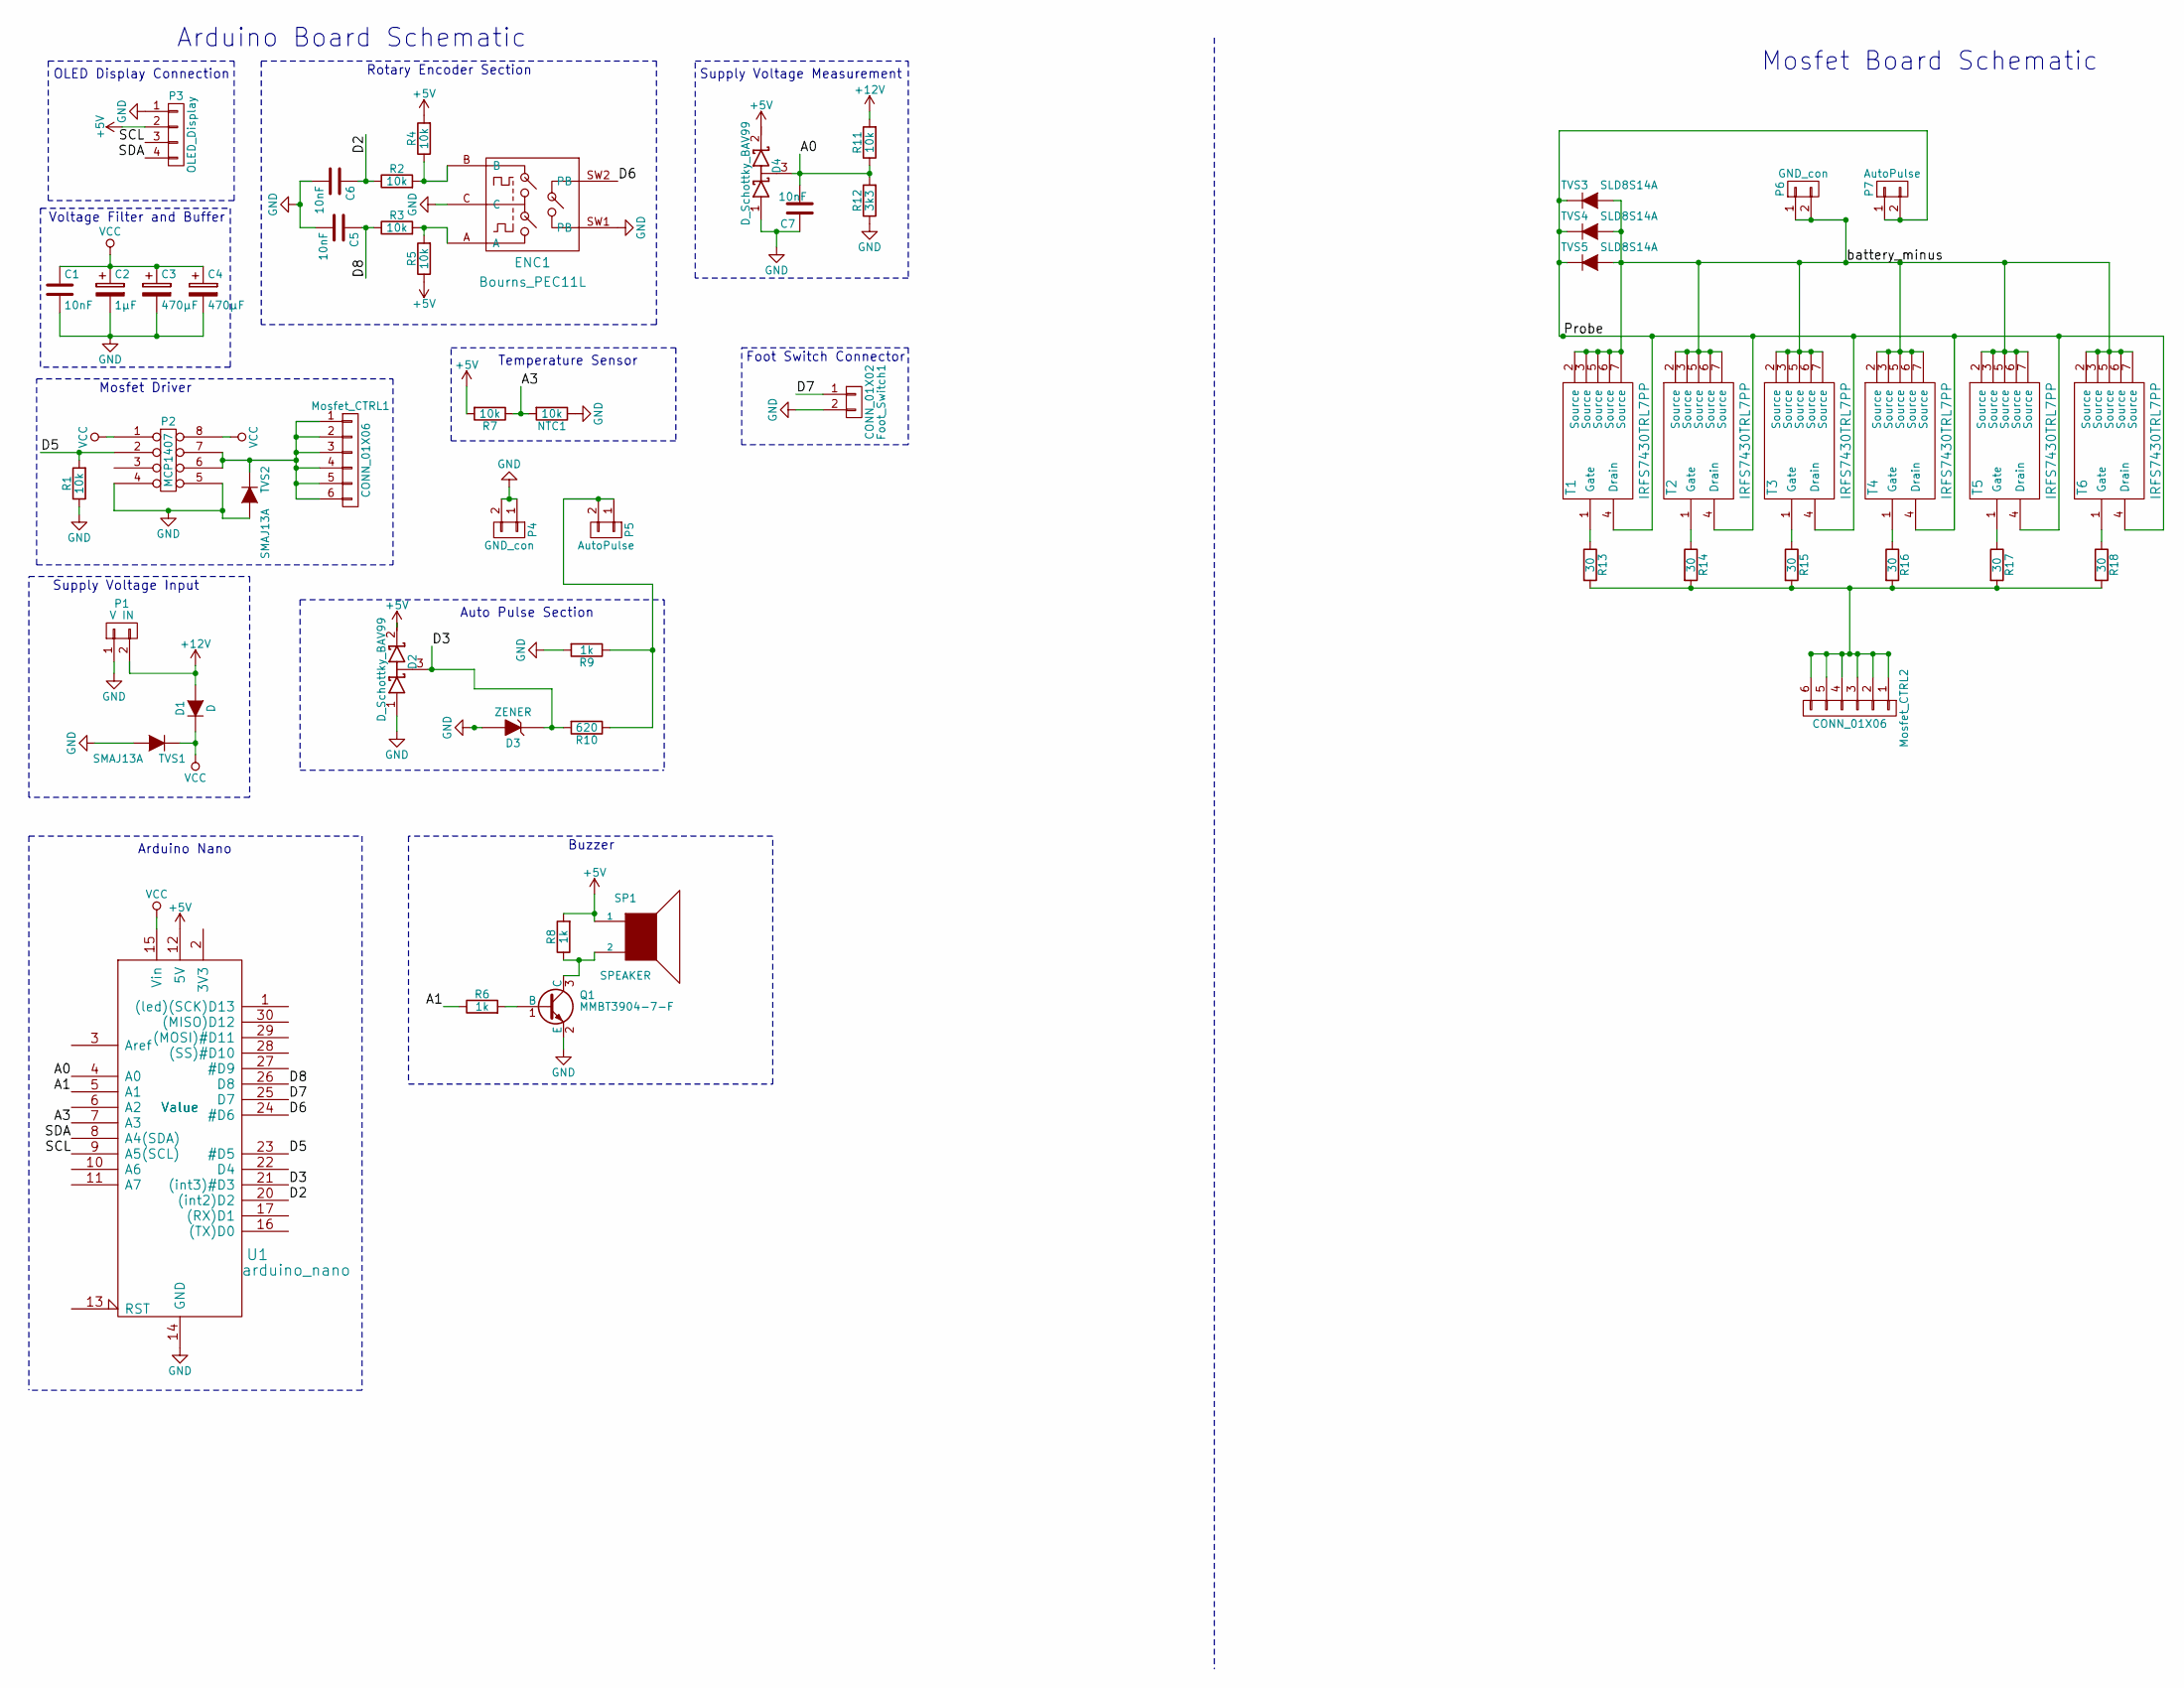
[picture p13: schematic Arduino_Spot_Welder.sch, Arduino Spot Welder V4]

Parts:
C1, C5: 10nF; C_0805_HandSoldering
C2: 1µF; C_Disc_D7.5mm_W5.0mm_P5.00mm
C3: 470µF; CP_Elec_10x10
C4: 470µF; CP_Elec_10x10; MFG Part Number Value
C6, C7: 10nF; C_0805_HandSoldering; MFG Part Number Value
D1: D; D_SMA
D2, D4: D_Schottky_BAV99; SOT-23; MFG Part Number BAV99Q-7-F
D3: ZENER; D_SOD-123
ENC1: Bourns_PEC11L; ALPS_STEC12E08; MFG Part Number PEC11L-4220F-S0015
Foot_Switch1: CONN_01X02; Molex_KK-6410-02_02x2.54mm_Straight
Mosfet_CTRL1, Mosfet_CTRL2: CONN_01X06; Pin_Header_Straight_1x06_Pitch2.54mm
NTC1: 10k; R_0805_HandSoldering; MFG Part Number NCP21XV103J03RA
P1: V IN; Terminal_Block_2P_3.5mm; MFG Part Number Value
P2: MCP1407; SOIC-8_3.9x4.9mm_Pitch1.27mm; MFG Part Number MCP1407-E/SN
P3: OLED_Display; OLED_SSD1306_128x64
P4, P6: GND_con; Pin_Header_Straight_1x02_Pitch2.54mm
P5, P7: AutoPulse; Pin_Header_Straight_1x02_Pitch2.54mm
Q1: MMBT3904-7-F; SOT-23; MFG Part Number MMBT3904-7-F
R1, R2, R3, R4, R5, R11: 10k; R_0805_HandSoldering
R6, R8, R9: 1k; R_0805_HandSoldering; MFG Part Number Value
R7: 10k; R_0805_HandSoldering; MFG Part Number Value
R10: 620; R_0805_HandSoldering
R12: 3k3; R_0805_HandSoldering; MFG Part Number Value
R13, R14, R15, R16, R17, R18: 30; R_1206_HandSoldering
SP1: SPEAKER; Buzzer_PS1240P02BT; MFG Part Number PS1240P02BT
T1, T2, T3, T4, T5, T6: IRFS7430TRL7PP; TO-263-6
TVS1, TVS2: SMAJ13A; D_SMA; MFG Part Number SMAJ13A-13-F
TVS3, TVS4, TVS5: SLD8S14A; SMTO-263; MFG Part Number SLD8S14A
U1: arduino_nano; arduino_mini; MFG Part Number Value

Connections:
+5V: D2.2 (K), D4.2 (K), P3.2, R4.2, R5.1, R7.2, R8.2, SP1.1, U1.12 (5V)
+12V: D1.2 (A), P1.2, R11.2
/A0: C7.2, D4.3 (common), R11.1, R12.2, U1.4 (A0)
/A1: R6.1, U1.5 (A1)
/A3: NTC1.2, R7.1, U1.7 (A3)
/D2: C6.1, R2.1, U1.20 ((int2)D2)
/D3: D2.3 (common), D3.1 (K), R10.2, U1.21 ((int3)#D3)
/D5: P2.2, R1.2, U1.23 (#D5)
/D6: ENC1.SW2 (PB), U1.24 (#D6)
/D7: Foot_Switch1.1, U1.25 (D7)
/D8: C5.1, R3.1, U1.26 (D8)
/Probe: P7.1, P7.2, T1.4 (Drain), T2.4 (Drain), T3.4 (Drain), T4.4 (Drain), T5.4 (Drain), T6.4 (Drain), TVS3.1 (K), TVS4.1 (K), TVS5.1 (K)
/SCL: P3.3, U1.9 (A5(SCL))
/SDA: P3.4, U1.8 (A4(SDA))
/battery_minus: P6.1, P6.2, T1.2 (Source), T1.3 (Source), T1.5 (Source), T1.6 (Source), T1.7 (Source), T2.2 (Source), T2.3 (Source), T2.5 (Source), T2.6 (Source), T2.7 (Source), T3.2 (Source), T3.3 (Source), T3.5 (Source), T3.6 (Source), T3.7 (Source), T4.2 (Source), T4.3 (Source), T4.5 (Source), T4.6 (Source), T4.7 (Source), T5.2 (Source), T5.3 (Source), T5.5 (Source), T5.6 (Source), T5.7 (Source), T6.2 (Source), T6.3 (Source), T6.5 (Source), T6.6 (Source), T6.7 (Source), TVS3.2 (A), TVS4.2 (A), TVS5.2 (A)
GND: C1.2, C2.2, C3.2, C4.2, C5.2, C6.2, C7.1, D2.1 (A), D3.2 (A), D4.1 (A), ENC1.C, ENC1.SW1 (PB), Foot_Switch1.2, NTC1.1, P1.1, P2.4, P2.5, P3.1, P4.1, P4.2, Q1.2 (E), R1.1, R9.2, R12.1, TVS1.2 (A), TVS2.2 (A), U1.14 (GND), U1.19 (GND)
unnamed: ENC1.A, R3.2, R5.2
unnamed: ENC1.B, R2.2, R4.1
unnamed: Mosfet_CTRL1.1, Mosfet_CTRL1.2, Mosfet_CTRL1.3, Mosfet_CTRL1.4, Mosfet_CTRL1.5, Mosfet_CTRL1.6, P2.6, P2.7, TVS2.1 (K)
unnamed: Mosfet_CTRL2.1, Mosfet_CTRL2.2, Mosfet_CTRL2.3, Mosfet_CTRL2.4, Mosfet_CTRL2.5, Mosfet_CTRL2.6, R13.2, R14.2, R15.2, R16.2, R17.2, R18.2
unnamed: P5.1, P5.2, R9.1, R10.1
unnamed: Q1.1 (B), R6.2
unnamed: Q1.3 (C), R8.1, SP1.2
unnamed: R13.1, T1.1 (Gate)
unnamed: R14.1, T2.1 (Gate)
unnamed: R15.1, T3.1 (Gate)
unnamed: R16.1, T4.1 (Gate)
unnamed: R17.1, T5.1 (Gate)
unnamed: R18.1, T6.1 (Gate)
VCC: C1.1, C2.1, C3.1, C4.1, D1.1 (K), P2.1, P2.8, TVS1.1 (K), U1.15 (Vin)

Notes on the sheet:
Arduino Board Schematic
Mosfet Board Schematic
Auto Pulse Section
OLED Display Connection
Rotary Encoder Section
Supply Voltage Measurement
Supply Voltage Input
Buzzer
Mosfet Driver
Voltage Filter and Buffer
Foot Switch Connector
Arduino Nano
Temperature Sensor

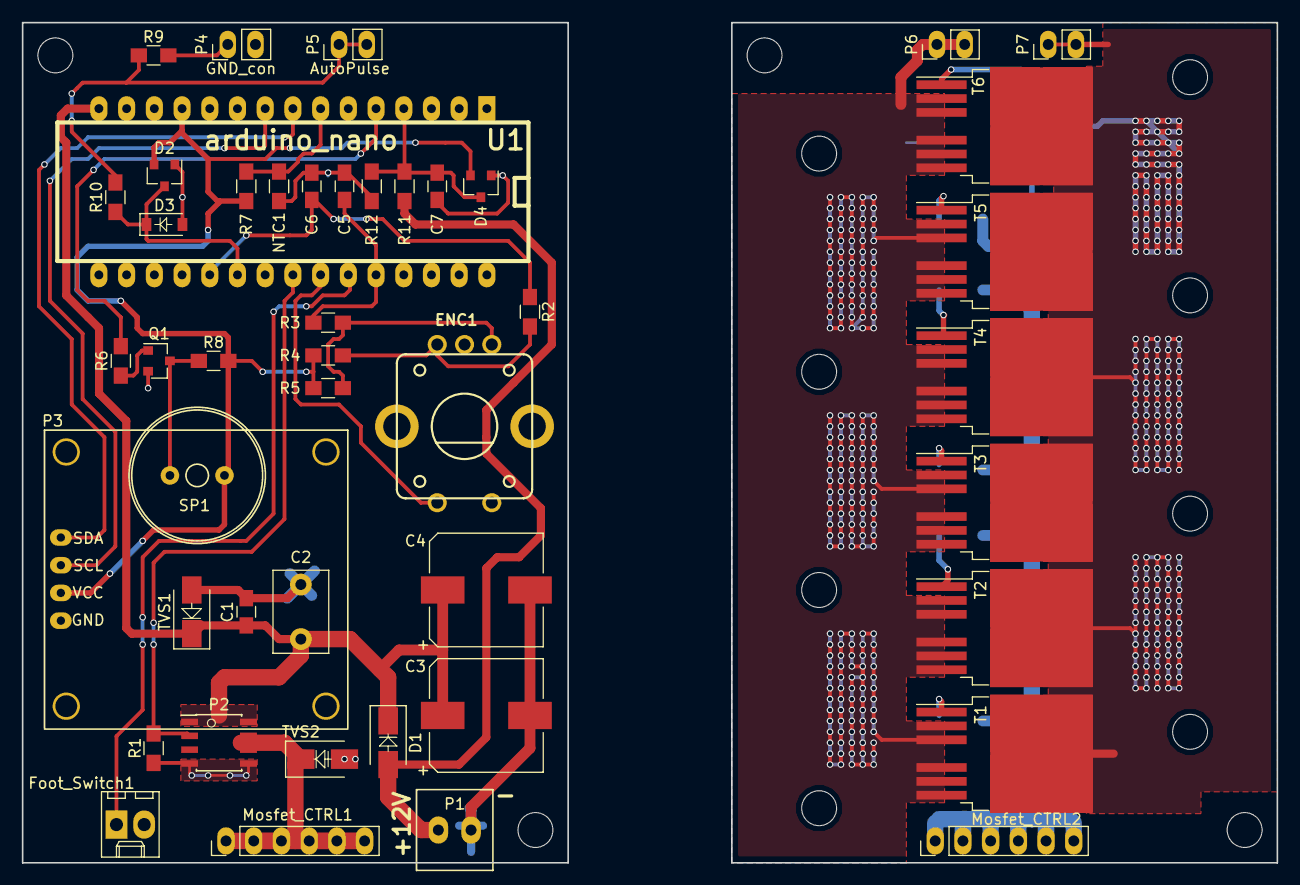
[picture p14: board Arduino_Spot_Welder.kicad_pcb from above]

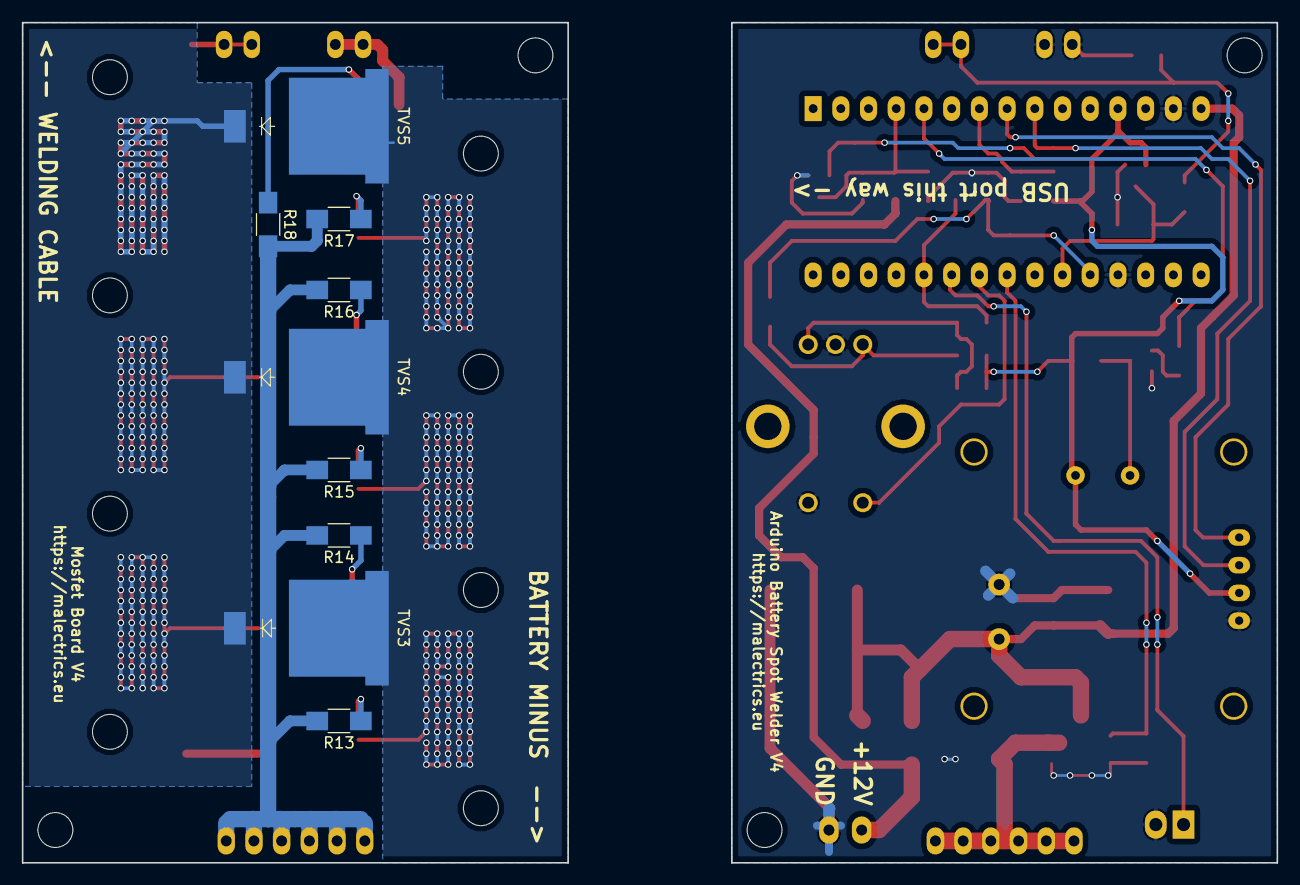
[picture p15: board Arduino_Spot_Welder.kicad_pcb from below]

Board: 2 copper layers, 115.0 x 77.0 mm, 55 parts (9 on the bottom side), 30 nets.

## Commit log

2021-08-18 Create Readme.md
    These are the gerber files for the Arduino PCB V4. This one can be ordered with the standard 1oz copper layer.
2021-08-18 Create Readme.md
    These are the Gerber files for the Mosfet PCB V4. Please order it with 4oz copper layer at the pcb manufacturer because it needs to take a lot of current.
2026-05-12 Update purchase links for Arduino and OLED display
